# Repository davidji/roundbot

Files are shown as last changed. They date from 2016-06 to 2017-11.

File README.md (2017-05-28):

This is a 3D printable robot with MBED control software. It uses signal processing to reduce the component count normally associated with quadrature encoding.

There are also lots of other objects defined in [Solid Python](https://github.com/SolidCode/SolidPython) loosely associated with the project

The build and all the dependencies for the software come from [PlatformIO](http://platformio.org/).

The 3D models require [Solid Python](https://github.com/SolidCode/SolidPython) and [OpenSCAD](http://www.openscad.org/)

TODO: The hardware needs some explanation

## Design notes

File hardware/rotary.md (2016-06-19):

A rotary encoder generates two signals. Going forward, one signal will
be 90 degrees forward of the other, and going in reverse, the opposite.

If the signal was digital, the rising edge of one signal could trigger 
an interrupt which captures the value of the other signal which can be
used to determine the direction.

The capture needs to happen within 1/8th of the period of the encoder
signal to be reliable.

The motor could run up to 30K RPM, The encoders have 3 arms or 5 arms, 
I think this means the signal is 3x or 5x the frequency of the motor.
This is (30K/60)*5 = 2.5KHz, so the period is 400us.

mbed only offers one way of sampling - which is ask for a sample and
wait until it's done, but the STM32F303K8 can complete a sample in 0.2us!
Even if mbed is insanely inefficient, I should be able to do this without
any additional hardware: I can use the ADC and signal processing.

400us/8 = 50us. I need to sample every 50us in order to be within 1/8th of the
zero crossing. When that happens, I do another sample.

It's worth just checking how many instructions get executed in 50us -
at 72MHz it's about 350. That's not a huge number.

Notice the hardware could just sample both channels on a schedule,
and interrupt the application on completion. If I used Chibios I
could easily do this.

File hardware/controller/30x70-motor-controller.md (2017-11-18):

Motor controller with low voltage cutoff, reverse voltage protection
and push on/push off switch.

Calculation for divider resistors

VS = switch voltage i.e. the switch off voltage = 6.6V minimum
VD1 = voltage drop across the diode D1

R4/(R4 + R7) <= 1.24/(VS - VD1)

I'm going to pick R4 = 15K

That means the current at the switching voltage will be 1.24/15K = 0.08mA so VD1 ~ 0.5V

(R4 + R7)/R4 >= (VS - VD1)/1.24
R7 >= R4*(VS - VD1)/1.24 - R4
   >= 15K*6.1/1.24 - 15K
   >= 58K
   = 62K (E24)

VS = 1.24*(R4+R7)/R4 + VD1
   = 6.865V

That's OK. Also, If I choose R2 = 68K

VS2 = The minimum switch on voltage
    = 1.24*(R4+R2)/R4
    = 6.861V

which matches very closely.

The cathode current for IC1 (TS432A) is determined by R1. It needs to be > 80uA. The maximum value for
R1 at 6.6V is then 82K. I seem to be getting away with less - and that's because the typical
minimum is actually 20uA, but there's no point relying on that.

The application circuit for the TS43A most like mine is the series pass regulator - because
there's in effect no load. It has a capacitor between the cathode and reference, which
wasn't in my first version of the design.

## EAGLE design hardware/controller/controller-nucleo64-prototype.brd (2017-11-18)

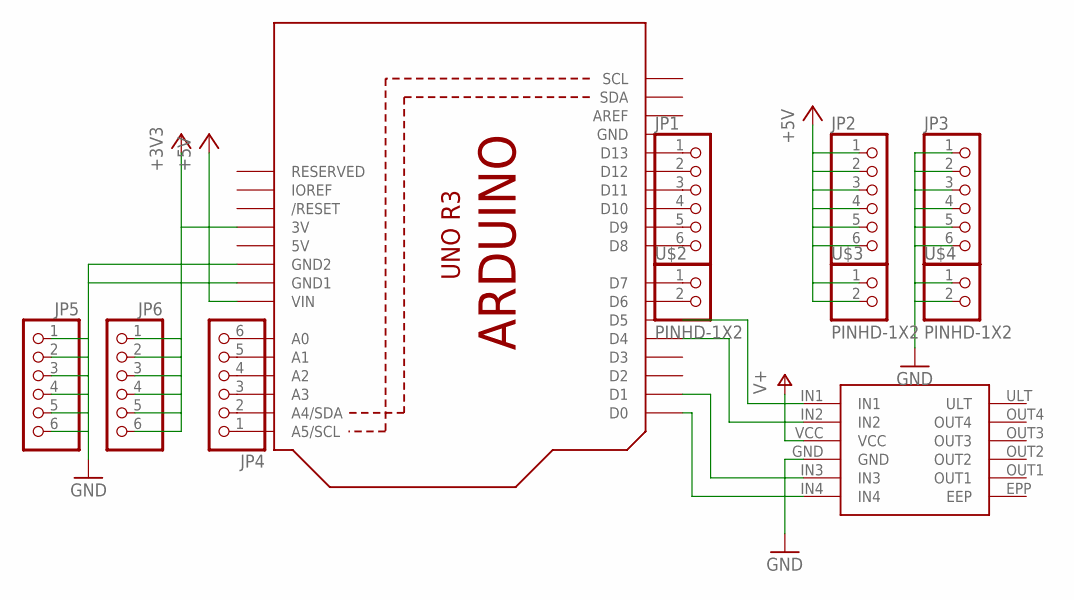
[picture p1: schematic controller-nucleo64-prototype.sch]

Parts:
JP1, JP2, JP3, JP4, JP5, JP6: PINHD-1X6CB; 1X06-CLEANBIG
U1: ARDUINOR3-DIMENSION; ARDUINOR3
U$1: DRV8833-MODULEUPSIDE-DOWN; DRV8833-BRKOUT-INV
U$2, U$3, U$4: PINHD-1X2; 1X02-CLEANBIG

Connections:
5V: U1.5V
+3V3: JP6.1, JP6.2, JP6.3, JP6.4, JP6.5, JP6.6, U1.3V
+5V: JP2.1, JP2.2, JP2.3, JP2.4, JP2.5, JP2.6, U1.VIN, U$3.1, U$3.2
GND: JP3.1, JP3.2, JP3.3, JP3.4, JP3.5, JP3.6, JP5.1, JP5.2, JP5.3, JP5.4, JP5.5, JP5.6, U1.GND, U1.GND1, U1.GND2, U$1.GND, U$4.1, U$4.2
unnamed: U1.D0, U$1.IN4
unnamed: U1.D1, U$1.IN3
unnamed: U1.D4, U$1.IN2
unnamed: U1.D5, U$1.IN1
unnamed: JP1.1, U1.D13
unnamed: JP1.2, U1.D12
unnamed: JP1.3, U1.D11
unnamed: JP1.4, U1.D10
unnamed: JP1.5, U1.D9
unnamed: JP1.6, U1.D8
unnamed: JP4.1, U1.A5 (A5/SCL)
unnamed: JP4.2, U1.A4 (A4/SDA)
unnamed: JP4.3, U1.A3
unnamed: JP4.4, U1.A2
unnamed: JP4.5, U1.A1
unnamed: JP4.6, U1.A0
unnamed: U1.D7, U$2.1
unnamed: U1.D6, U$2.2
V+: U$1.VCC

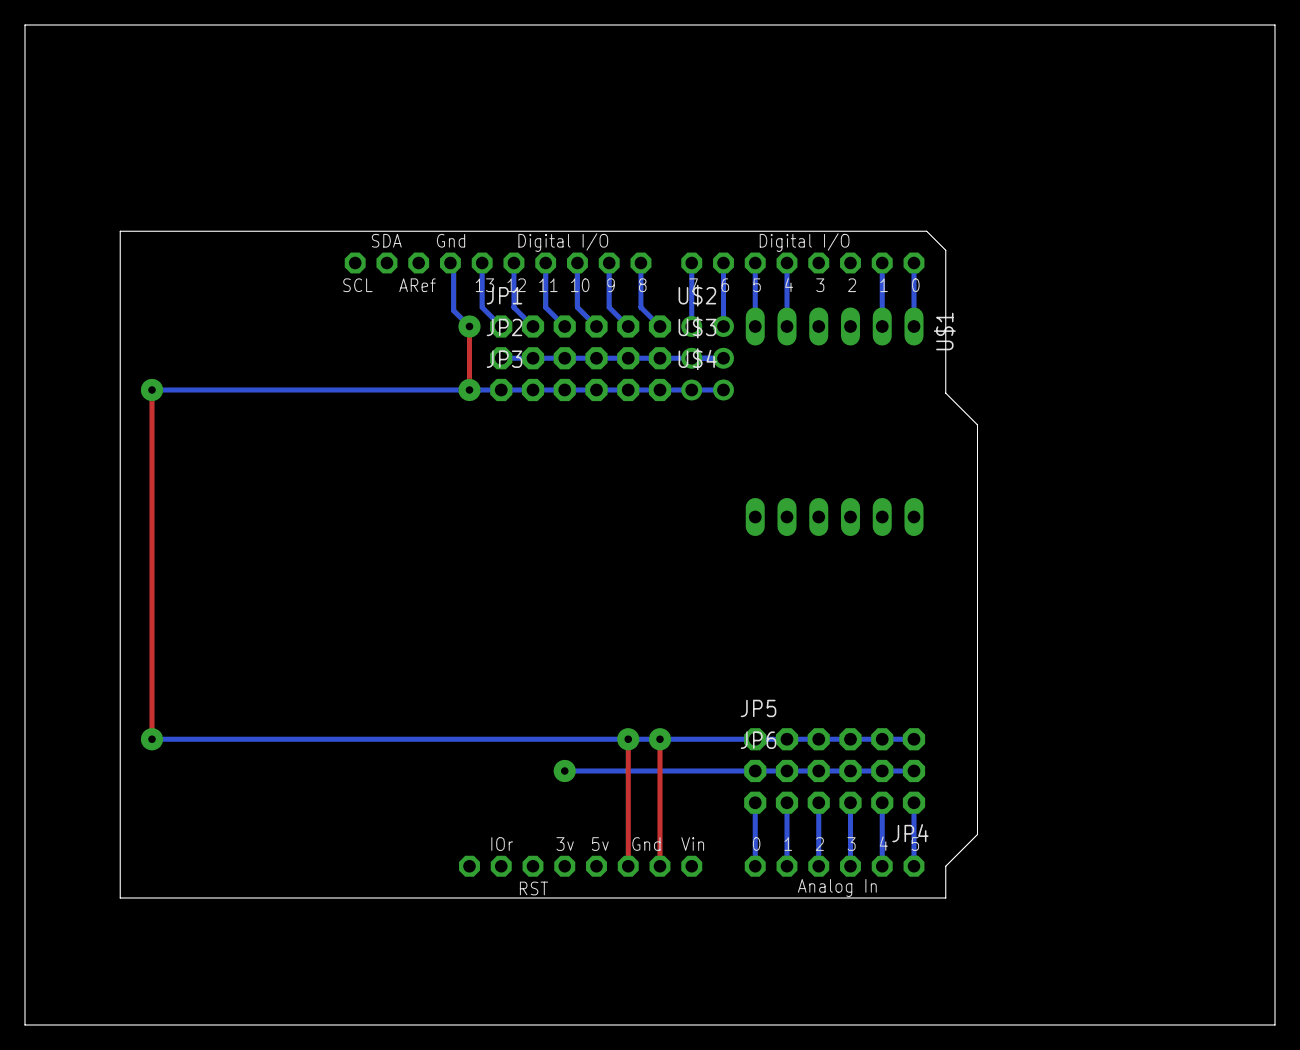
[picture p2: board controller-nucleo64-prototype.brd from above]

Board: 2 copper layers, 100.0 x 80.0 mm, 11 parts (0 on the bottom side), 21 nets.

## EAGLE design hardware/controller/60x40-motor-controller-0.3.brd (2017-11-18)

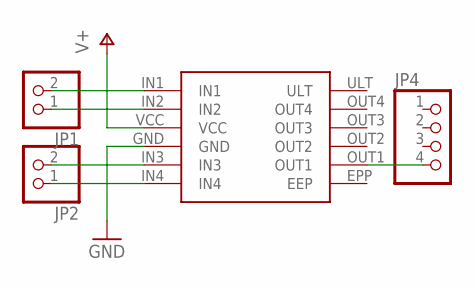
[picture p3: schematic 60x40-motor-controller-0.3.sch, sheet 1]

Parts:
JP1, JP2: PINHD-1X2/90; 1X02/90
JP4: PINHD-1X4/90; 1X04/90
U$1: DRV8833-MODULE; DRV8833-BRKOUT

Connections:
GND: U$1.GND; also elsewhere on the board
unnamed: JP2.2, U$1.IN3
unnamed: JP2.1, U$1.IN4
unnamed: JP1.2, U$1.IN1
unnamed: JP1.1, U$1.IN2
unnamed: JP4.4, U$1.OUT1
V+: U$1.VCC; also elsewhere on the board

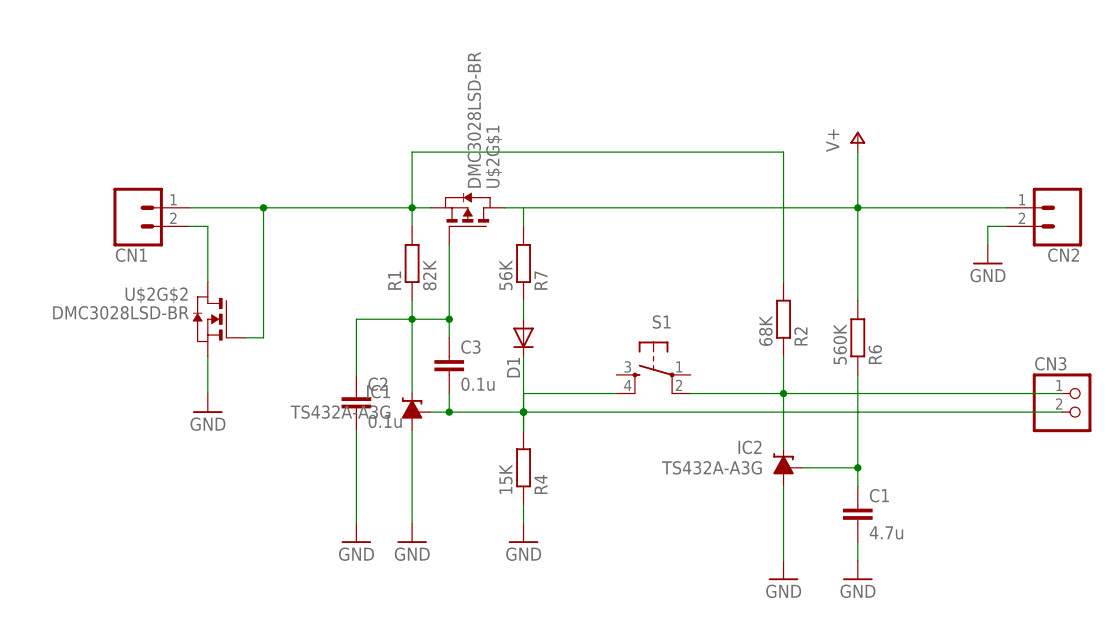
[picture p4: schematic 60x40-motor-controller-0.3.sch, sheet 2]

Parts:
C1: 4.7u; C025-025X050
C2, C3: 0.1u; C025-024X044
CN1, CN2: CONN_02-JST-XTH; JST-2-XTH
CN3: PINHD-1X2/90; 1X02/90
D1: DIODE-D-5; D-5
IC1, IC2: TS432A-A3G; TO92-LINE
R1: 82K; 0204V
R2: 68K; 0204/7
R4: 15K; 0204V
R6: 560K; 0207/10
R7: 56K; 0204V
S1: PROTO-MICRO-SWITCH; B3F-10XX-PROTO
U$2: DMC3028LSD-BR; DIL8-BREAKOUT

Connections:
GND: C1.2, C2.2, CN2.2, IC1.2 (A), IC2.2 (A), R4.1, U$2.1 (S); also elsewhere on the board
unnamed: CN1.1, R1.2, R2.2, U$2.2 (G), U$2.3 (S)
unnamed: C2.1, C3.1, IC1.1 (C), R1.1, U$2.4 (G)
unnamed: CN1.2, U$2.7 (D), U$2.8 (D)
unnamed: C3.2, CN3.2, D1.C, IC1.3 (FB), R4.2, S1.4 (S1)
unnamed: CN3.1, IC2.1 (C), R2.1, S1.2 (P1)
unnamed: C1.1, IC2.3 (FB), R6.1
unnamed: D1.A, R7.1
V+: CN2.1, R6.2, R7.2, U$2.5 (D), U$2.6 (D); also elsewhere on the board

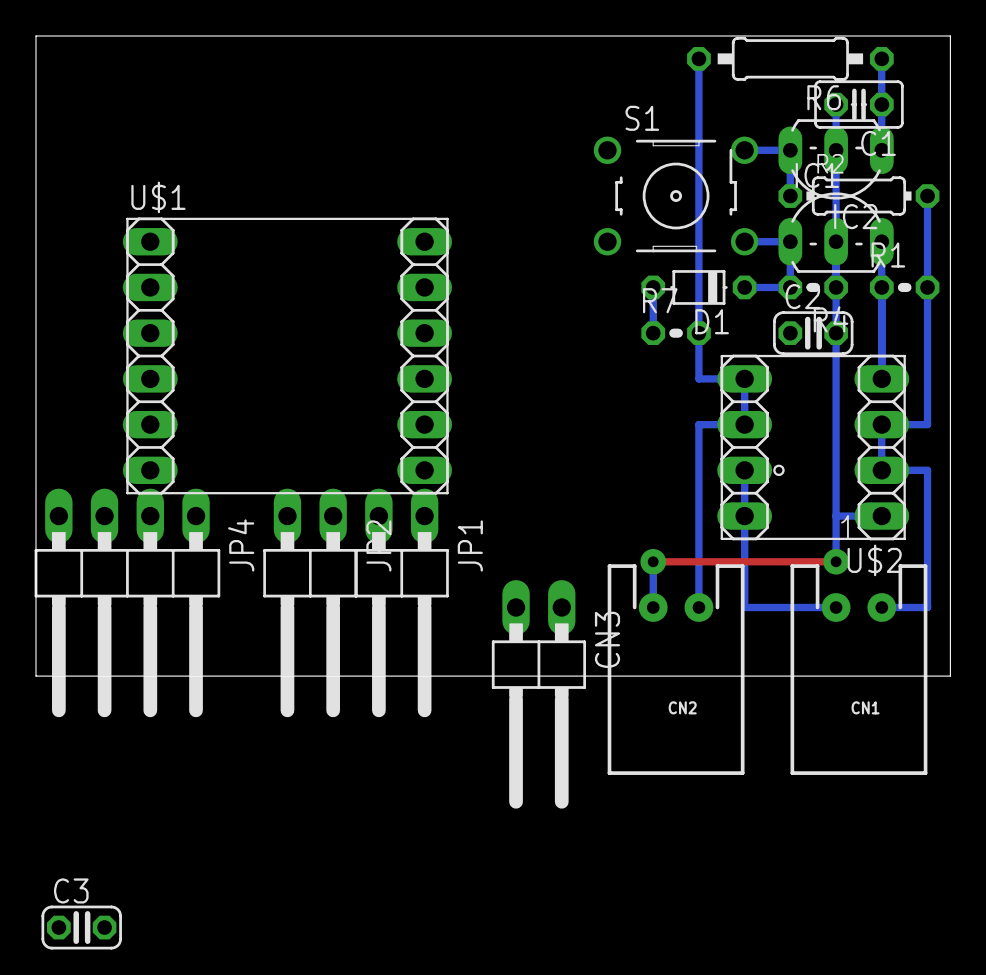
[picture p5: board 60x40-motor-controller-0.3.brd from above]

Board: 2 copper layers, 50.8 x 35.6 mm, 20 parts (0 on the bottom side), 14 nets.

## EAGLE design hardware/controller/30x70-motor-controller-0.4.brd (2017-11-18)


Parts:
JP1, JP2: PINHD-1X2/90; 1X02/90
JP4: PINHD-1X4/90; 1X04/90
U$1: DRV8833-MODULE; DRV8833-BRKOUT

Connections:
GND: U$1.GND; also elsewhere on the board
unnamed: JP2.2, U$1.IN3
unnamed: JP2.1, U$1.IN4
unnamed: JP1.2, U$1.IN1
unnamed: JP1.1, U$1.IN2
unnamed: JP4.4, U$1.OUT1
V+: U$1.VCC; also elsewhere on the board

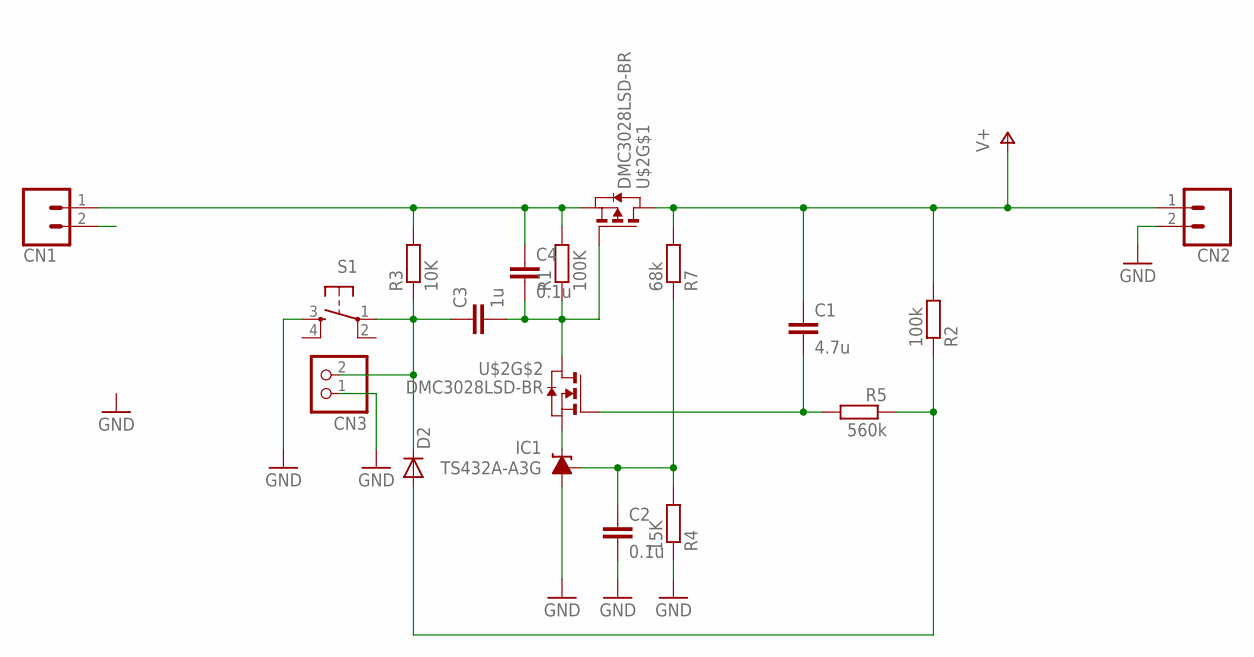
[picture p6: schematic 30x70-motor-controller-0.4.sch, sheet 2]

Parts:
C1: 4.7u; C025-025X050
C2, C4: 0.1u; C025-024X044
C3: 1u; C025-024X044
CN1, CN2: CONN_02-JST-XTH; JST-2-XTH
CN3: PINHD-1X2/90; 1X02/90
D2: DIODE-D-2.5; D-2.5
IC1: TS432A-A3G; TO92-LINE
R1: 100K; 0204V
R2: 100k; 0204V
R3: 10K; 0204V
R4: 15K; 0204V
R5: 560k; 0204/7
R7: 68k; 0204/7
S1: PROTO-MICRO-SWITCH; B3F-10XX-PROTO
U$2: DMC3028LSD-BR; DIL8-BREAKOUT

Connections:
GND: C2.2, CN2.2, CN3.1, IC1.2 (A), R4.1, S1.3 (S); also elsewhere on the board
unnamed: C4.1, CN1.1, R1.2, R3.2, U$2.3 (S)
unnamed: C3.2, C4.2, R1.1, U$2.4 (G), U$2.7 (D), U$2.8 (D)
unnamed: C2.1, IC1.3 (FB), R4.2, R7.1
unnamed: C1.2, R5.2, U$2.2 (G)
unnamed: D2.A, R2.1, R5.1
unnamed: IC1.1 (C), U$2.1 (S)
unnamed: C3.1, CN3.2, D2.C, R3.1, S1.1
V+: C1.1, CN2.1, R2.2, R7.2, U$2.5 (D), U$2.6 (D); also elsewhere on the board

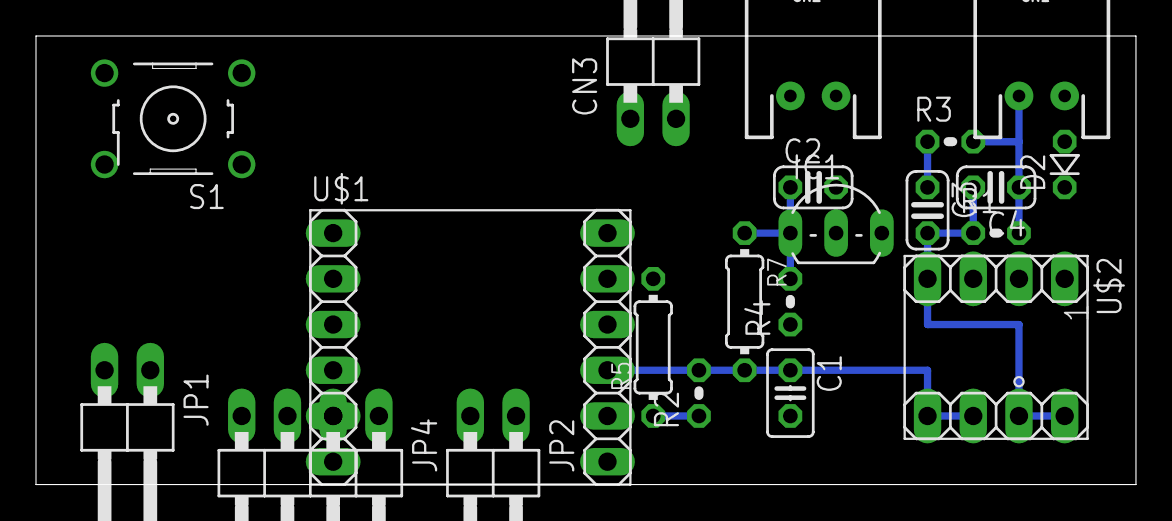
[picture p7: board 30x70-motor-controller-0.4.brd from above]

Board: 2 copper layers, 61.1 x 24.9 mm, 21 parts (0 on the bottom side), 14 nets.

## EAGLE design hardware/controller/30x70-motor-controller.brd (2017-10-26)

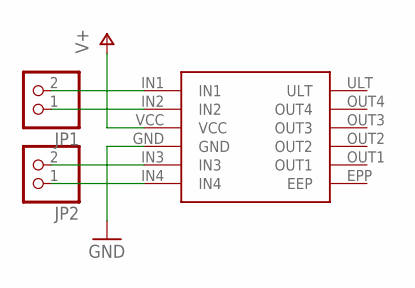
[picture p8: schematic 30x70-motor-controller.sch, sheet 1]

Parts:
JP1, JP2: PINHD-1X2/90; 1X02/90
U$1: DRV8833-MODULE; DRV8833-BRKOUT

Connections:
GND: U$1.GND; also elsewhere on the board
unnamed: JP2.2, U$1.IN3
unnamed: JP2.1, U$1.IN4
unnamed: JP1.2, U$1.IN1
unnamed: JP1.1, U$1.IN2
V+: U$1.VCC; also elsewhere on the board

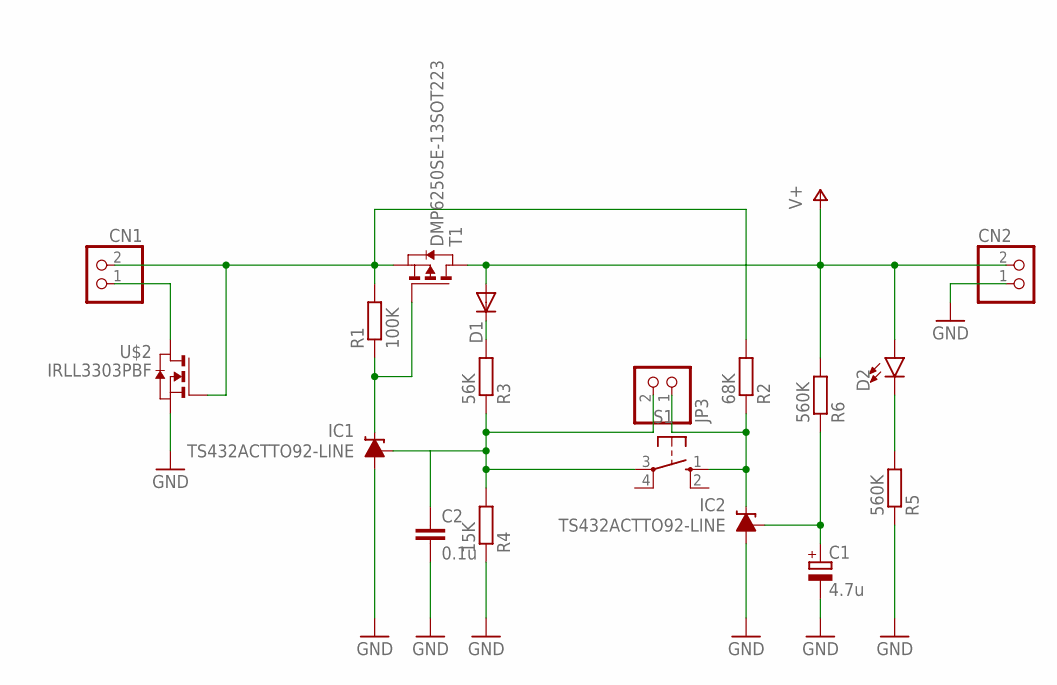
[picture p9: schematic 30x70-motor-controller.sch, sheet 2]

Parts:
C1: 4.7u; E2,5-5
C2: 0.1u; C025-024X044
CN1, CN2: JST_2PIN-THM-RA; JST-PH-2-THM-RA
D1: DIODE-D-2.5; D-2.5
D2: LED-3MM-NO_SILK; LED_3MM-NS
IC1, IC2: TS432ACTTO92-LINE; TO92-LINE
JP3: PINHD-1X2/90; 1X02/90
R1: 100K; 0204/5
R2: 68K; 0204/5
R3: 56K; 0204/5
R4: 15K; 0204V
R5, R6: 560K; 0204/5
S1: 10-XX; B3F-10XX
T1: DMP6250SE-13SOT223; SOT223
U$2: IRLL3303PBF; SOT223

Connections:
GND: C1.-, C2.2, CN2.1 (2), IC1.2 (A), IC2.2 (A), R4.1, R5.1, U$2.3 (S); also elsewhere on the board
unnamed: CN1.2 (1), R1.2, R2.2, T1.3 (S), U$2.1 (G)
unnamed: IC1.1 (C), R1.1, T1.1 (G)
unnamed: CN1.1 (2), U$2.2 (D), U$2.4 (D)
unnamed: C2.1, IC1.3 (FB), JP3.2, R3.1, R4.2, S1.3
unnamed: IC2.1 (C), JP3.1, R2.1, S1.1 (S)
unnamed: C1.+, IC2.3 (FB), R6.1
unnamed: D1.C, R3.2
unnamed: D2.K (C), R5.2
V+: CN2.2 (1), D1.A, D2.A, R6.2, T1.2 (D), T1.4 (D); also elsewhere on the board

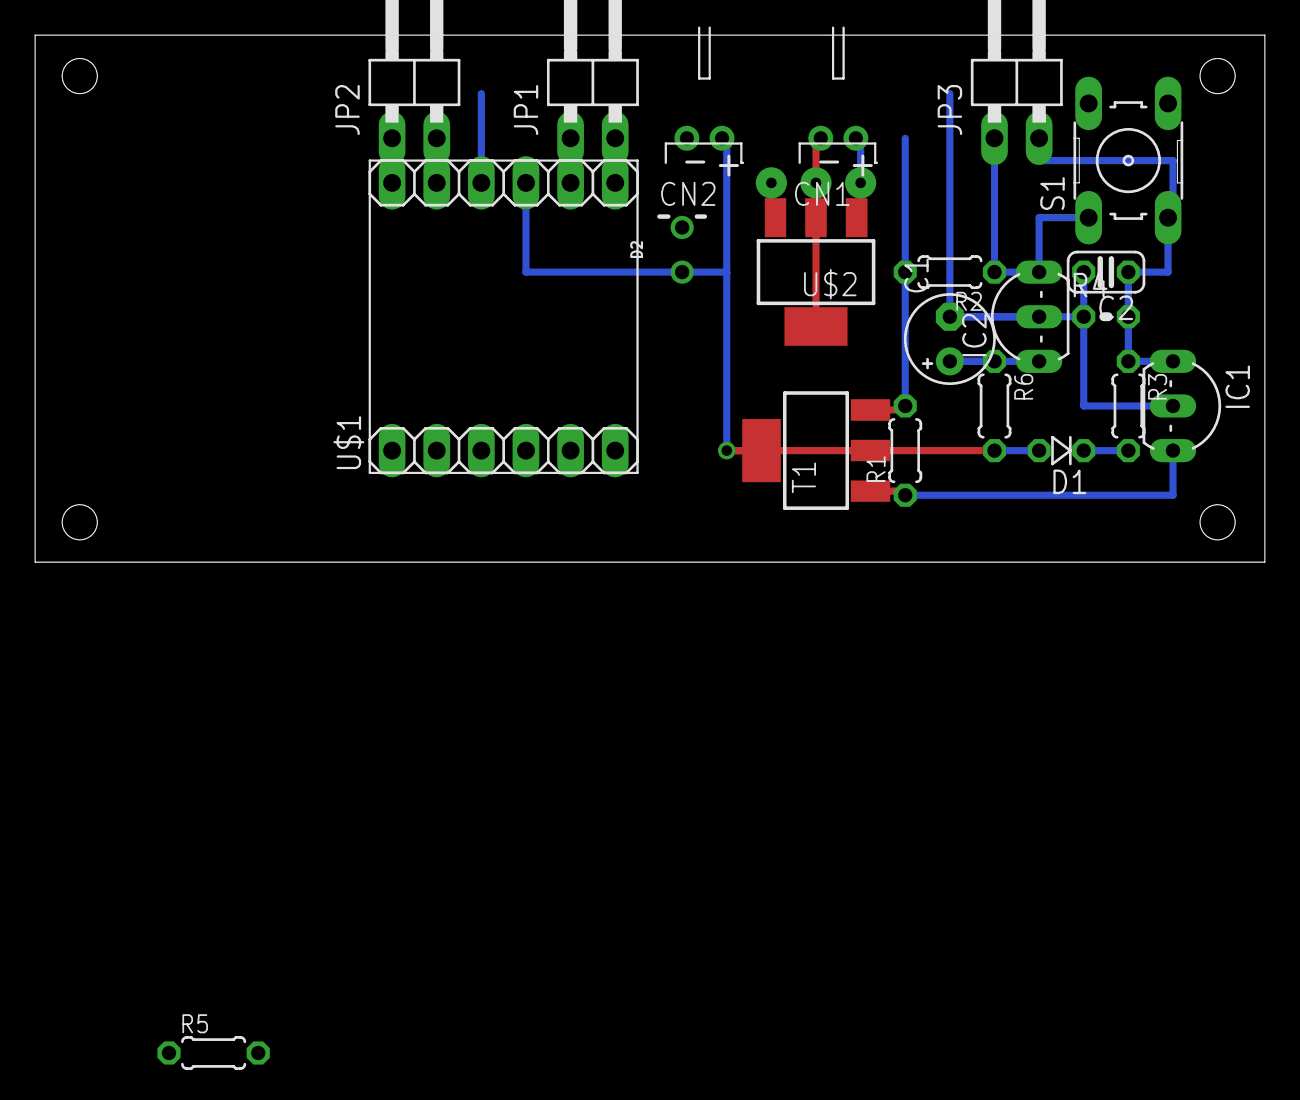
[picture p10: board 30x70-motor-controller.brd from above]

Board: 2 copper layers, 70.0 x 30.0 mm, 21 parts (0 on the bottom side), 14 nets.

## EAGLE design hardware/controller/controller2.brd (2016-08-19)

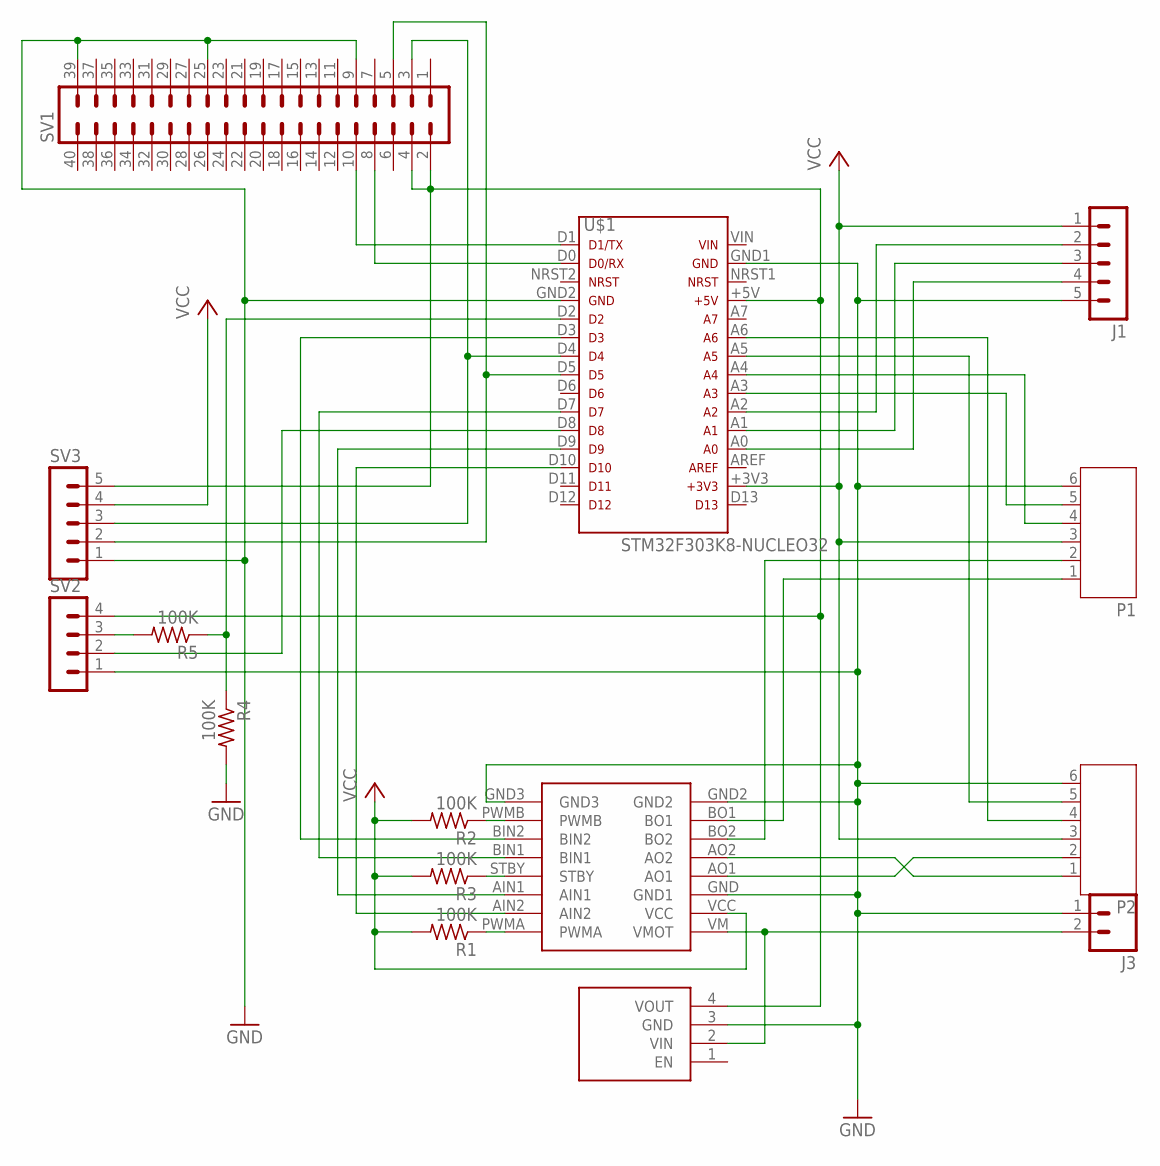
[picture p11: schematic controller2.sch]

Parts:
J1: MA05-1
J3: M02JST-PTH-VERT; JST-2-PTH-VERT
P1, P2: JST-PH6
R1, R2, R3, R4, R5: 100K; M0805
SV1: MA20-2
SV2: MA04-1
SV3: MA05-1
U$1: STM32F303K8-NUCLEO32; NUCLEO32
U$2: TB6612FNG-CARRIER/SPARKFUN; TB6612FNG-BRKOUT/SPARKFUN
U$3: S7V8A; S7V8

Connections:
GND: J1.5, J3.1, P1.6, P2.6, R4.2, SV1.9, SV1.25, SV1.39, SV2.1, SV3.1, U$1.GND1, U$1.GND2, U$2.GND (GND1), U$2.GND2, U$2.GND3, U$3.3 (GND)
unnamed: U$1.D3, U$2.BIN2
unnamed: U$1.D7, U$2.BIN1
unnamed: U$1.D9, U$2.AIN1
unnamed: U$1.D10, U$2.AIN2
unnamed: P2.2, U$2.AO1
unnamed: R2.1, U$2.PWMB
unnamed: R1.1, U$2.PWMA
unnamed: R3.1, U$2.STBY
unnamed: P2.1, U$2.AO2
unnamed: P1.2, U$2.BO2
unnamed: P1.1, U$2.BO1
unnamed: SV1.3, SV3.3, U$1.D4
unnamed: SV1.5, SV3.2, U$1.D5
unnamed: SV1.8, U$1.D0
unnamed: SV1.10, U$1.D1
unnamed: J3.2, U$2.VM (VMOT), U$3.2 (VIN)
unnamed: P1.4, U$1.A4
unnamed: P1.5, U$1.A3
unnamed: P2.4, U$1.A6
unnamed: P2.5, U$1.A5
unnamed: J1.2, U$1.A2
unnamed: J1.3, U$1.A1
unnamed: J1.4, U$1.A0
unnamed: R5.2, SV2.3
unnamed: SV1.2, SV1.4, SV2.4, SV3.5, U$1.+5V, U$3.4 (VOUT)
unnamed: R4.1, R5.1, U$1.D2
unnamed: SV2.2, U$1.D8
VCC: J1.1, P1.3, P2.3, R1.2, R2.2, R3.2, SV3.4, U$1.+3V3, U$2.VCC

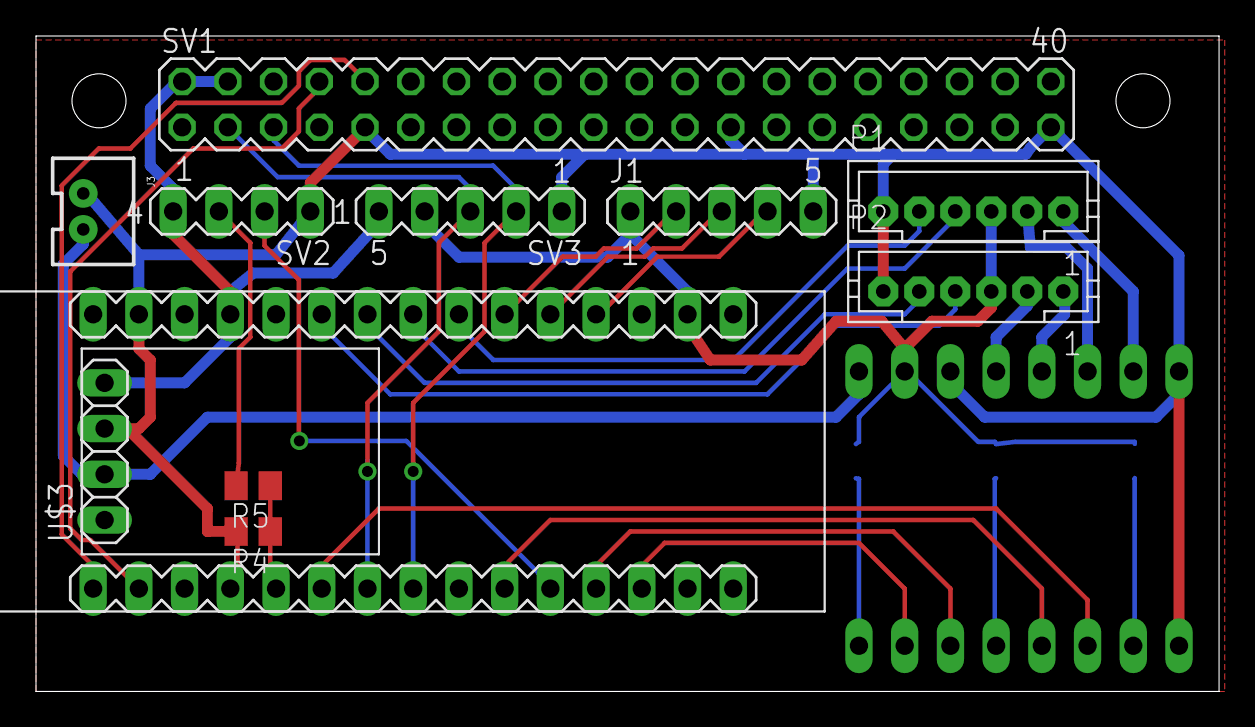
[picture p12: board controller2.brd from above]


Board: 2 copper layers, 65.7 x 36.4 mm, 15 parts (4 on the bottom side), 29 nets.

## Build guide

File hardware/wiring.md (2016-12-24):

I'm using an STM32F303K8 Nucleo board for GPIO. It's functions are

 - PWM motor control (2 PWM, 4 GPIO)
 - rotary encoder feedback ADC channels 4
 - analog reflectance sensors ADC channels x3
 - ultrasonic rangefinder sensor Timer x1 one in channel, one out channel
 - status LED dislay Timer x1 one out channel
 - Serial interface to raspberry PI
 - NRF24 via SPI + 2GPIO

See https://developer.mbed.org/platforms/ST-Nucleo-F303K8/

Here are all the options for each pin

MCU  |MBED | Function
-----|-----|----------
PA9  | D1  | TSC_G4_IO1, TIM1_CH2, USART1_TX, TIM15_BKIN, TIM2_CH3
PA10 | D0  | TIM17_BKIN, TSC_G4_IO2, TIM1_CH3, USART1_RX, COMP6_OUT, TIM2_CH4
PA12 | D2  | TIM16_CH1, TIM1_CH2N, USART1_RTS_DE, COMP2_OUT, CAN_TX, TIM1_ETR
PB0  | D3  | TIM3_CH3, TSC_G3_IO2, TIM1_CH2N
PB7  | D4  | TIM17_CH1N, TSC_G5_IO4, I2C1_SDA, USART1_RX, TIM3_CH4
PB6  | D5  | TIM16_CH1N, TSC_G5_IO3, I2C1_SCL, USART1_TX
PB1  | D6  | TIM3_CH4, TSC_G3_IO3, TIM1_CH3N, COMP4_OUT
PF0  | D7  | TIM1_CH3N
PF1  | D8  |
PA8  | D9  | TIM1_CH1, USART1_CK
PA11 | D10 | TIM1_CH1N, USART1_CTS, CAN_RX, TIM1_CH4, TIM1_BKIN2
PB5  | D11 | TIM16_BKIN, TIM3_CH2, I2C1_SMBA, SPI1_MOSI, USART2_CK, TIM17_CH
PB4  | D12 | TIM16_CH1, TIM3_CH1, TSC_G5_IO2, SPI1_MISO, USART2_RX, TIM17_BKIN
PA2  | A7  | ADC1_IN3, COMP2_INM, TIM2_CH3, TSC_G1_IO3, USART2_TX, COMP2_OUT, TIM15_CH1
PA7  | A6  | ADC2_IN4, COMP2_INP, OPAMP2_VINP, TIM17_CH1, TIM3_CH2, TSC_G2_IO4, SPI1_MOSI, TIM1_CH1N
PA6  | A5  | ADC2_IN3, DAC2_OUT1, OPAMP2_VOUT, TIM16_CH1, TIM3_CH1, TSC_G2_IO3, SPI1_MISO, TIM1_BKIN
PA5  | A4  | ADC2_IN2, DAC1_OUT2, OPAMP2_VINM, TIM2_CH1/TI M2_ETR, TSC_G2_IO2, SPI1_SCK
PA4  | A3  | ADC2_IN1, DAC1_OUT1, COMP2_INM4, COMP4_INM4, COMP6_INM4, TIM3_CH2, TSC_G2_IO1, SPI1_NSS, USART2_CK
PA3  | A2  | ADC1_IN4, TIM2_CH4, TSC_G1_IO4, USART2_RX, TIM15_CH2
PA1  | A1  | ADC1_IN2, TIM2_CH2, TSC_G1_IO2, USART2_RTS_DE, TIM15_CH1N
PA0  | A0  | ADC1_IN1, TIM2_CH1/TI M2_ETR, TSC_G1_IO1, USART2_CTS
PB3  | D13 | SWO, TIM2_CH2, TSC_G5_IO1, SPI1_SCK, USART2_TX, TIM3_ETR, ADC2_IN12, COMP4_INM, TSC_G3_IO4

TIM2,TIM3: Motor control
TIM1: WS2812
ADC1: Rotary encoders
ADC2: Reflectance sensors
SPI1: RF24

MCU  | MBED| Function  | Used
-----|-----|-----------|----------
PA9  | D1  | USART1_TX | Serial TX
PA10 | D0  | USART1_RX | Serial RX
PA12 | D2  |           | Unused
PB0  | D3  | TIM1_CH2N | Motor L IN1
PB7  | D4  | I2C1_SDA  | I2C Raspberry Pi/other
PB6  | D5  | I2C1_SCL  | I2C Raspberry Pi/other
PB1  | D6  |           | Unused
PF0  | D7  | TIM1_CH3N | Motor L IN2
PF1  | D8  |           | Unused
PA8  | D9  | TIM1_CH1  | Motor R IN1
PA11 | D10 | TIM1_CH4  | Motor R IN2
PB5  | D11 | SPI_MOSI  | RF24 MOSI
PB4  | D12 | SPI_MISO  | RF24 MISO
PA2  | A7  |           | Unused
PA7  | A6  | ADC2_IN4  | Rotary encoder R2
PA6  | A5  | ADC2_IN3  | Rotary encoder R1
PA5  | A4  | ADC2_IN2  | Rotary encoder L2
PA4  | A3  | ADC2_IN1  | Rotary encoder L1
PA3  | A2  | ADC1_IN4  | Reflectance 3
PA1  | A1  | ADC1_IN2  | Reflectance 2
PA0  | A0  | ADC1_IN1  | Reflectance 1
PB3  | D13 | SPI1_SCK  | RF24 SCK

An alternative board is

https://developer.mbed.org/platforms/ST-Nucleo-F303RE/

MCU  |MBED | Function
-----|-----|----------
A2   | D1  | TIM2_CH3, TSC_G1_IO3, USART2_TX, COMP2_OUT, TIM15_CH1, ADC1_IN3, COMP2_INM, OPAMP1_VOUT 
PA3  | D0  | TIM2_CH4, TSC_G1_IO4, USART2_RX, TIM15_CH2
PA10 | D2  | TIM17_BKIN, TSC_G4_IO2, I2C2_SDA, SPI2_MISO, I2S2ext_SD, TIM1_CH3, USART1_RX, COMP6_OUT, TIM2_CH4, TIM8_BKIN
PB3  | D3  | TIM2_CH2, TIM4_ETR, TSC_G5_IO1, TIM8_CH1N, SPI1_SCK, SPI3_SCK, I2S3_CK, USART2_TX, TIM3_ETR
PB5  | D4  | TIM16_BKIN, TIM3_CH2, TIM8_CH3N, I2C1_SMBAl, SPI1_MOSI, SPI3_MOSI, I2S3_SD, USART2_CK, I2C3_SDA, TIM17_CH1
PB4  | D5  | TIM16_CH1, TIM3_CH1, TSC_G5_IO2, TIM8_CH2N, SPI1_MISO, SPI3_MISO, I2S3ext_SD, USART2_RX, TIM17_BKIN
PB10 | D6  | TIM2_CH3, TSC_SYNC, USART3_TX,COMP5_INM, OPAMP3_VINM, OPAMP4_VINM
PA8  | D7  | MCO, I2C3_SCL, I2C2_SMBAL, I2S2_MCK, TIM1_CH1, USART1_CK, COMP3_OUT, TIM4_ETR
PA9  | D8  | I2C3_SMBAL, TSC_G4_IO1, I2C2_SCL, I2S3_MCK, TIM1_CH2, USART1_TX, COMP5_OUT, TIM15_BKIN, TIM2_CH3
PC7  | D9  | TIM3_CH2, TIM8_CH2, I2S3_MCK, COMP5_OUT
PB6  | D10 | TIM16_CH1N, TIM4_CH1, TSC_G5_IO3, I2C1_SCL, TIM8_CH1, TIM8_ETR, USART1_TX, TIM8_BKIN2
PA7  | D11 | TIM17_CH1, TIM3_CH2, TSC_G2_IO4, TIM8_CH1N, SPI1_MOSI, TIM1_CH1N, ADC2_IN4, COMP2_INP, OPAMP1_VINP, OPAMP2_VINP
PA6  | D12 | TIM16_CH1, TIM3_CH1, TSC_G2_IO3, TIM8_BKIN, SPI1_MISO, TIM1_BKIN, COMP1_OUT, ADC2_IN3, OPAMP2_VOUT
PA5  | D13 | TIM2_CH1, TIM2_ETR, TSC_G2_IO2, SPI1_SCK, ADC2_IN2, DAC1_OUT2, COMP1_INM, COMP2_INM, COMP3_INM, COMP4_INM, COMP5_INM, COMP6_INM, COMP7_INM, OPAMP1_VINP, OPAMP2_VINM, OPAMP3_VINP
PB9  | D14 | TIM17_CH1, TIM4_CH4, I2C1_SDA, IR-OUT, USART3_TX, COMP2_OUT, CAN_TX, TIM8_CH3
PB8  | D15 | TIM16_CH1, TIM4_CH3, TSC_SYNC, I2C1_SCL, USART3_RX, COMP1_OUT, CAN_RX, TIM8_CH2, TIM1_BKIN
PC0  | A5  | TIM1_CH1, ADC12_IN6, COMP7_INM
PC1  | A4  | TIM1_CH2, ADC12_IN7, COMP7_INP
PB0  | A3  | TIM3_CH3, TSC_G3_IO2, TIM8_CH2N, TIM1_CH2N, ADC3_IN12, COMP4_INP, OPAMP2_VINP, OPAMP3_VINP
PA4  | A2  | TIM3_CH2, TSC_G2_IO1, SPI1_NSS, SPI3_NSS, I2S3_WS, USART2_CK, ADC2_IN1, DAC1_OUT1, COMP1_INM, COMP2_INM, COMP3_INM, COMP4_INM, COMP5_INM, COMP6_INM, COMP7_INM, OPAMP4_VINP
PA1  | A1  | TIM2_CH1, TIM2_ETR, TSC_G1_IO1, USART2_CTS, COMP1_OUT, TIM8_BKIN, TIM8_ETR, ADC1_IN2, COMP1_INP, OPAMP1_VINP, OPAMP3_VINP
PA0  | A0  | TIM2_CH1, TIM2_ETR, TSC_G1_IO1, USART2_CTS, COMP1_OUT,
TIM8_BKIN, TIM8_ETR, ADC1_IN1, COMP1_INM, RTC_TAMP2, WKUP1

MCU  |MBED | Function  | Used
-----|-----|-----------|--------------
PB3  | D3  | SPI3 SCLK | SPI NRF24
PB5  | D4  | SPI3 MOSI | SPI NRF24
PB4  | D5  | SPI3 MISO | SPI NRF24
PB10 | D6  | GPIO      | Soft switch out
PA8  | D7  | PWM       | Motor
PA9  | D8  | PWM       | Motor
PC7  | D9  | PWM       | Motor
PB6  | D10 | PWM       | Motor
PA7  | D11 | Analog In | Battery voltage
PA6  | D12 | GPIO      | Soft switch in
PB9  | D13 | I2C1 SDA  | I2C
PB8  | D14 | I2C1 SCL  | I2C

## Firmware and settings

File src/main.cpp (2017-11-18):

#define _USE_MATH_DEFINES

#include <functional>
#include <math.h>
#include <stdlib.h>
#include <stddef.h>
#include <string.h>
#include "mbed.h"
#include "motor.h"
#include "differential.h"
#include "VL53L0X.h"

#include "Spki.h"
#include "CanonicalInput.h"
#include "FloatPair.h"
#include "Tag.h"
#include "TagDispatcher.h"
#include "SlipInput.h"
#include "SlipOutput.h"
#include "MBedStreamWrapper.h"

#include "wiring.h"

using namespace sexps;
using namespace slip;
using namespace motor;

Serial serial(serial_tx_pin, serial_rx_pin, 115200);
MBedStreamWrapper serialwrapper(serial);
SlipInput requests(serialwrapper);
SlipOutput responses(serialwrapper);


const float pi = 3.1415927;
const float gearMotorRatio = 50.0;
const int encoderArms = 3;
const float wheelDiameter = 0.032;
const float wheelBase = 0.083;
const float stepLength = (pi*wheelDiameter)/(gearMotorRatio*encoderArms);

// Break/drive mode gives nice linear response, but the first 10% produces little to no movement.
MotorOut leftMotor(motor_left_in1_pin, motor_left_in2_pin, BRAKE, 0.1, 1.0);
MotorOut rightMotor(motor_right_in1_pin, motor_right_in2_pin, BRAKE, 0.1, 1.0);
MotorEncoder leftEncoder(rotary_encoder_left_a_pin, rotary_encoder_left_b_pin);
MotorEncoder rightEncoder(rotary_encoder_right_a_pin, rotary_encoder_right_b_pin);

DifferentialDrive differential(
		Wheel(leftMotor, leftEncoder, stepLength),
		Wheel(rightMotor, rightEncoder, stepLength), wheelBase);

Timer testTimer;
DigitalOut led1(LED1);
I2C i2c(i2c_sda_pin, i2c_scl_pin);
// Timer rangeTimer;
// VL53L0X range(&i2c, &rangeTimer);
// APDS9960 gesture(i2c);




void drive(float left, float right) {
    leftMotor.drive(left);
    rightMotor.drive(right);
}

int percent(float f) {
    return f * 100.0f;
}

CanonicalOutput &operator<<(CanonicalOutput &out, motor::MinMax &in) {
	out << tag("min", in.minimum);
	out << tag("max", in.maximum);
	return out;
}

CanonicalOutput &operator<<(CanonicalOutput &out, MotorEncoder &encoder) {
	out << encoder.in1;
	out << encoder.in2;
	return out;
}

CanonicalOutput &operator<<(CanonicalOutput &out, DifferentialDrive &d) {
	float left = d.left.peek();
	float right = d.right.peek();
	out << tag("left", left);
	out << tag("right", right);
	return out;
}

void motorsTestStep(float left, float right) {
    testTimer.reset();
    leftEncoder.read();
    rightEncoder.read();
    drive(left, right);
    wait_ms(1000);
    led1 = ~led1;
    float left_rotation = differential.left.read();
    float right_rotation = differential.right.read();
    float s = testTimer.read();

    responses.begin();
    CanonicalOutput out(responses);
    out << '(' << "test";
    out << '(' << "parameters";
    out << tag("left", left);
    out << tag("right", right);
    out << ')';
    out << tag("left", left_rotation);
    out << tag("right", right_rotation);
    out << tag("time", s);
    out << ')';
    responses.end();
}

void motorsTest(float speed) {
    testTimer.start();
    differential.start();
    motorsTestStep(0.0, 0.0); //stop
    motorsTestStep(speed, speed); // forward
    motorsTestStep(-speed, -speed); // backward
    motorsTestStep(speed, 0.0); // turn right
    motorsTestStep(0.0, speed); // turn left
    motorsTestStep(speed, -speed); // spin right
    motorsTestStep(-speed, speed); // spin left
    motorsTestStep(0.0, 0.0); //stop
    testTimer.stop();
    differential.stop();
}

void motorsTestSpeeds() {
    while(true) {
        for(int i = 1; i <= 4; ++i) {
            motorsTest(i*0.25);
        }
    }
}

void differential_test() {
    differential.start();

    // this little hack calibrates the encoders before we start the turns
    while (true) {
        differential.turn(pi/2.0);
        wait(3.0);
        differential.move(0.1);
        wait(3.0);
        led1.write(!led1.read());
    }
}

void encoder_test() {
    while (true) {
        motorsTestSpeeds();
    }
}

int mm(float m) {
    return m*1000;
}

class Shell {

public:

	bool invalid() {
		return false;
	}

	bool move(FloatPair &value) {
		differential.move(value);
		return true;
	}

	bool turn(FloatPair &value) {
		differential.turn(value);
		return true;
	}

	bool status() {
        responses.begin();
		CanonicalOutput out(responses);
		out << tag("progress", differential);
		responses.end();
        return true;
	}

	bool test() {
        motorsTestSpeeds();
        return true;
	}

	bool calibrate() {
        testTimer.start();
        for(float duty = 0; duty <= 1.0; duty = duty + 0.01) {
            motorsTestStep(duty, duty);
        }

        responses.begin();
		CanonicalOutput out(responses);
    	out << '(' << "encoders";
    	out << leftEncoder;
    	out << rightEncoder;
    	out << ')';
    	responses.end();

        return true;
	}


};

const auto dispatch = dispatcher(
		&Shell::invalid,
		tag("move", &Shell::move),
		tag("turn", &Shell::turn),
		tag("status", &Shell::status),
		tag("test", &Shell::test),
		tag("calibrate", &Shell::calibrate));

Shell commands;

void shell() {
	while(true) {
		CanonicalInput in(requests);
		bool result = dispatch.apply(commands, in);
		requests.next();
		responses.begin();
		CanonicalOutput encoder(responses);
		if (result) {
			int frames = requests.frames();
			encoder << tag("ok", frames);
		} else {
			if(in) {
				encoder << tag("error");
			} else {
				const char* message = in.message();
				encoder << tag("error", message);
			}
		}
		responses.end();
	}
}

int main() {
    i2c.frequency(400000);
    i2c.start();
    // range.init();
    // range.startContinuous();
    led1 = false;
    commands.test();
    led1 = false;

    shell();
}

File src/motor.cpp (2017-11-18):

#include "motor.h"
#include <math.h>

namespace motor {

MotorOut::MotorOut(PinName out1pin, PinName out2pin, MotorMode initial_mode, float min, float max)
: out1(PwmOut(out1pin)), out2(PwmOut(out2pin)),
  min_duty(min), max_duty(max) {
    out1.period_us(2500);
    out2.period_us(2500);
    mode(initial_mode);
    switch(default_mode) {
    case BRAKE:
        brake();
        break;
    case FREE:
        free();
        break;
    case DEFAULT:
    	break;
    }
}

void MotorOut::mode(MotorMode new_mode) {
    default_mode = new_mode == FREE ? FREE : BRAKE;
}

void MotorOut::free() {
    write(0.0, 0.0);
}

void MotorOut::brake() {
    write(1.0, 1.0);
}

void MotorOut::drive(float duty, MotorMode drive_mode) {
    float normalised = fabs(duty)*(max_duty - min_duty) + min_duty;
    switch(drive_mode) {
    case DEFAULT:
        drive(duty, default_mode);
        break;
    case FREE:
        if(duty < 0) {
            write(normalised, 0.0);
        } else if(duty > 0) {
            write(0.0, normalised);
        } else {
            free();
        }
        break;
    case BRAKE:
        if(duty < 0) {
            write(1.0 - normalised, 1.0);
        } else if(duty > 0) {
            write(1.0, 1.0 - normalised);
        } else {
            brake();
        }
        break;
    }
}

void MotorOut::write(float in1v, float in2v) {
    out1.write(in1v);
    out2.write(in2v);
}



MotorEncoder::MotorEncoder(PinName p1, PinName p2)
: in1(p1), in2(p2),
  ticker(),
  delta_r(0),
  count_s(0) {

}

MinMax::MinMax(PinName p)
: pin(p),
  zero(0.5),
  minimum(1.0),
  maximum(0.0) {
}

inline bool MinMax::update(float value) {
    if(maximum < value || minimum > value) {
        minimum = fmin(value, minimum);
        maximum = fmax(value, maximum);
        zero = (minimum + maximum)/2;
    }
    return value > zero;
}

void MotorEncoder::update(float in1v, float in2v) {
    count_s++;
    bool in1_next_value = in1.update(in1v);
    if(!in1_prev_value && in1_next_value) {
        bool in2_value = in2.update(in2v);
        delta_r += in2_value ? 1 : -1;
    }

    in1_prev_value = in1_next_value;
}

long MotorEncoder::read() {
    long delta = delta_r;
    delta_r = 0;
    return delta;
}

long MotorEncoder::peek() {
    return delta_r;
}

}; /* namespace motor */

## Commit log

2016-04-16 3 caster design leaving room for line following sensors at the front
2016-04-17 added drawing of caster mounts
2016-05-10 alternate 3d chassis, new flat chassis
2016-05-11 Reasonably complete laser cut version
2016-06-11 change wiring so nucleo serial port works
2016-06-11 add motor encoder support
2016-06-13 None of this works. about to switch to chibios
2016-06-17 It's important not to attach a function to the ticker before main() starts - it will just get disconnected
2016-06-18 track min and max for both channels, have separate zeros. This actually seems to be working now
2016-06-19 Get rid of the enable pins - they will just be pull up resistors. Fix a bug in break mode. Improvements in logging
    [main.cpp, motor.cpp]
2016-07-03 add eagle cad files for controller
    [controller.brd, controller.sch, controller2.brd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]
2016-08-19 auto ranging for rotary encoder, a few changes to the chassis, add rangefinder test
    [controller2.brd, controller2.sch]
2016-08-21 some corrections to the lid, ready for a new print, added a bit of lego support, finished off bulkhead for printing
    [lid.stl, rangebulkhead.scad, rangebulkhead.stl]
2016-08-31 This sort of works, in that it knows roughly when it's turned 1/4. It doesn't work, in that it makes no sense to use a pid controller this way.
    [rangebulkhead.scad, rangebulkhead.stl]
2016-09-22 RaspberryPi has M2.5 holes, add nucleo 64 mount points
2016-09-22 Compensate for friction, I think
    [motor-calibration.csv, motor-calibration.ods]
2016-12-04 Chassis changes for PETG + integral battery, motor mounts
2016-12-04 honeycomb base to reduce build plate adhesion, which is a problem for PETG
2016-12-24 Add time of flight, changes for platformio 3, switch to Nucleo F303RE
2017-01-27 Assorted 3d printed parts, switch to nucleo64 board
2017-02-11 Box for the nucleo-64 st-link board.
2017-05-28 Improvements to chassis: motor mount resists twisting better, cover for batteries to hold them in, flat top for easier composing of modules
2017-05-28 work in progress: head segment
    [lid.stl, rangebulkhead.scad, rangebulkhead.stl]
2017-06-01 A cage for module pcbs. A couple of different configurations, neither finalised
2017-06-16 A cover for a wifi piggy backed on a raspberry pi zero, using a split pin holder for the module
2017-06-16 A few feather wing related things
2017-06-16 A panel mount for a sub-miniture joystick
2017-06-16 various messing around with mounting the electronics in the chassis
2017-07-26 new layering of chassis to avoid lots of support material
2017-07-29 fix some bitrot: moveing to MBED 5?
    [main.cpp]
2017-07-30 This builds without RTOS. Building with RTOS doesn't work
    [main.cpp]
2017-08-03 something to attach all the electronics too, which is fairly agile
2017-10-26 mostly soft switch related stuff
    [30x70-motor-controller-0.2.brd, 30x70-motor-controller-0.2.sch, 30x70-motor-controller.brd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]
2017-10-26 model for a barrel dc connector I have a few of
2017-11-04 motor controller board
    [30x70-motor-controller-0.3.brd, 30x70-motor-controller-0.3.sch]
2017-11-18 Lots of controller designs
    [30x70-motor-controller-0.4.brd, 30x70-motor-controller-0.4.sch, 60x40-motor-controller-0.3.brd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]
2017-11-18 Various messing around trying to get mbed to do ADC fast enough

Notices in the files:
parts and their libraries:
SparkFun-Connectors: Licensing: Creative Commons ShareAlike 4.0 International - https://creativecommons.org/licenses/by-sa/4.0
